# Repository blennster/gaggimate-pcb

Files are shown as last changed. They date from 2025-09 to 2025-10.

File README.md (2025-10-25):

This is a reimplemenation of the gaggimate PCB. It is not officaly supported and never will be.

This work is in no way affiliated with the https://gaggimate.eu/ project.

## License

This work is licensed under CC BY-NC-SA 4.0. To view a copy of this license, visit https://creativecommons.org/licenses/by-nc-sa/4.0/

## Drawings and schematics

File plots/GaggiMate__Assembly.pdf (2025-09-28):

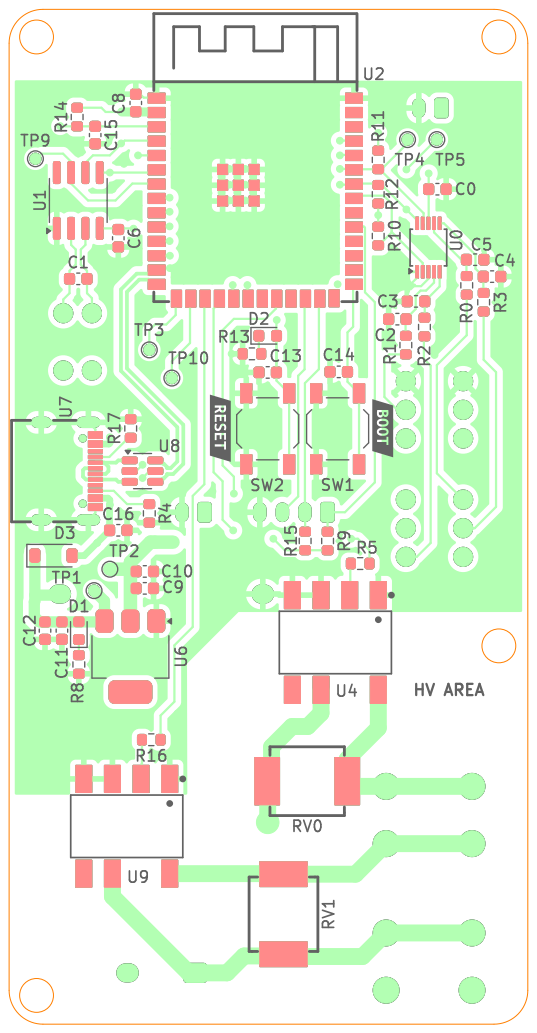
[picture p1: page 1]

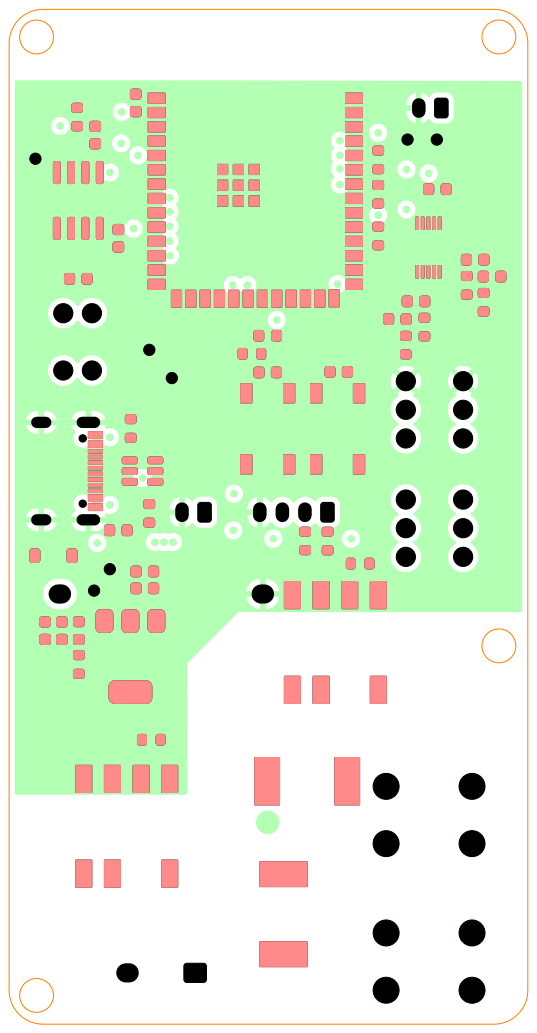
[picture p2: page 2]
D Date: KiCad; E.D.A. 9.0.4 Size: A4; Rev:; Id: /1 Title: File: GaggiMate.kicad_pcb Sheet: Colored; TOP-Copy Board2Pdf:; Colored; TOP-Copy -; Page 2/4

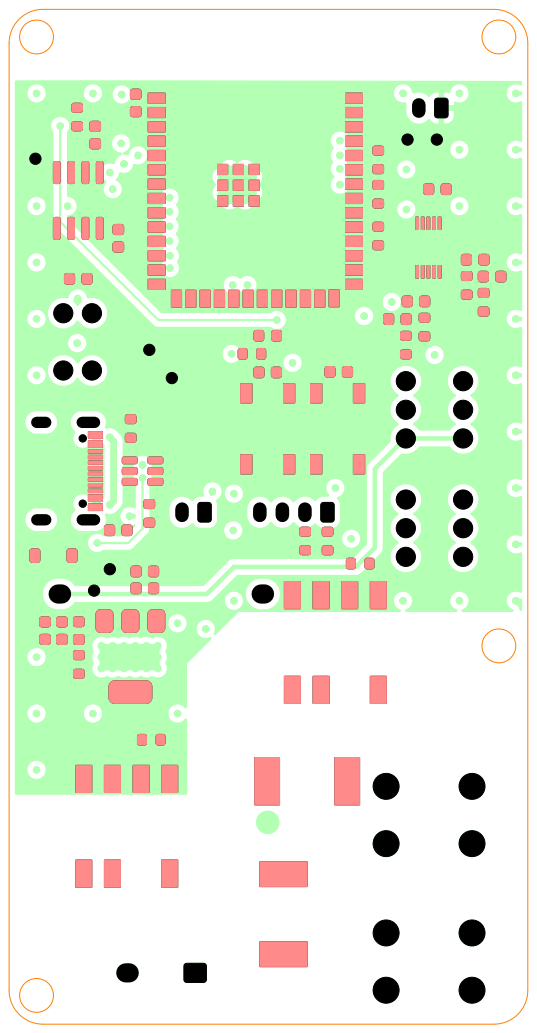
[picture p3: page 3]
D Date: KiCad; E.D.A. 9.0.4 Size: A4; Rev:; Id: /1 Title: File: GaggiMate.kicad_pcb Sheet: Colored; TOP-Copy-Copy Board2Pdf:; Colored; TOP-Copy-Copy; Page 3/4

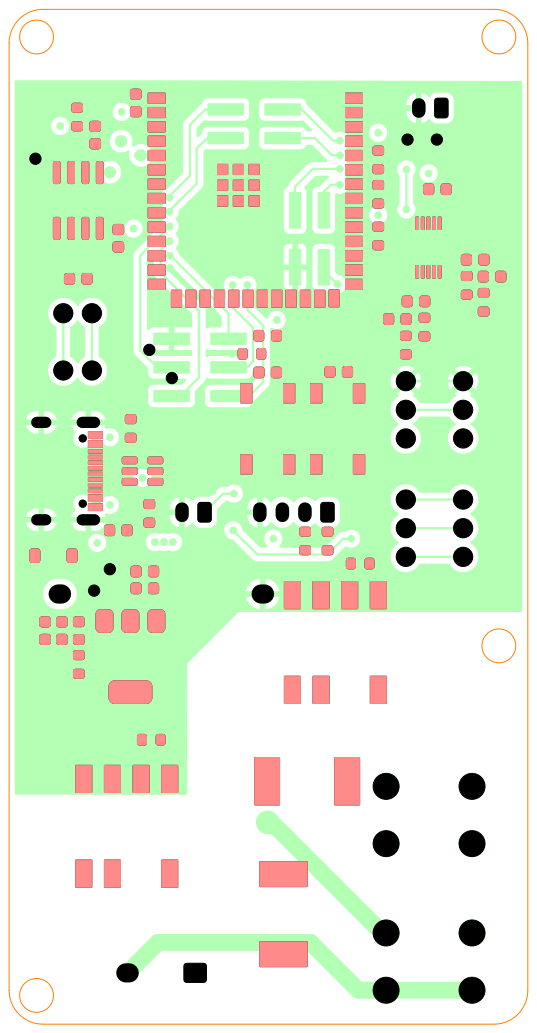
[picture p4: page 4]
D Date: KiCad; E.D.A. 9.0.4 Size: A4; Rev:; Id: /1 Title: File: GaggiMate.kicad_pcb Sheet: Colored; TOP-Copy-Copy-Copy Board2Pdf:; Colored; TOP-Copy-Copy-Copy; Page 4/4

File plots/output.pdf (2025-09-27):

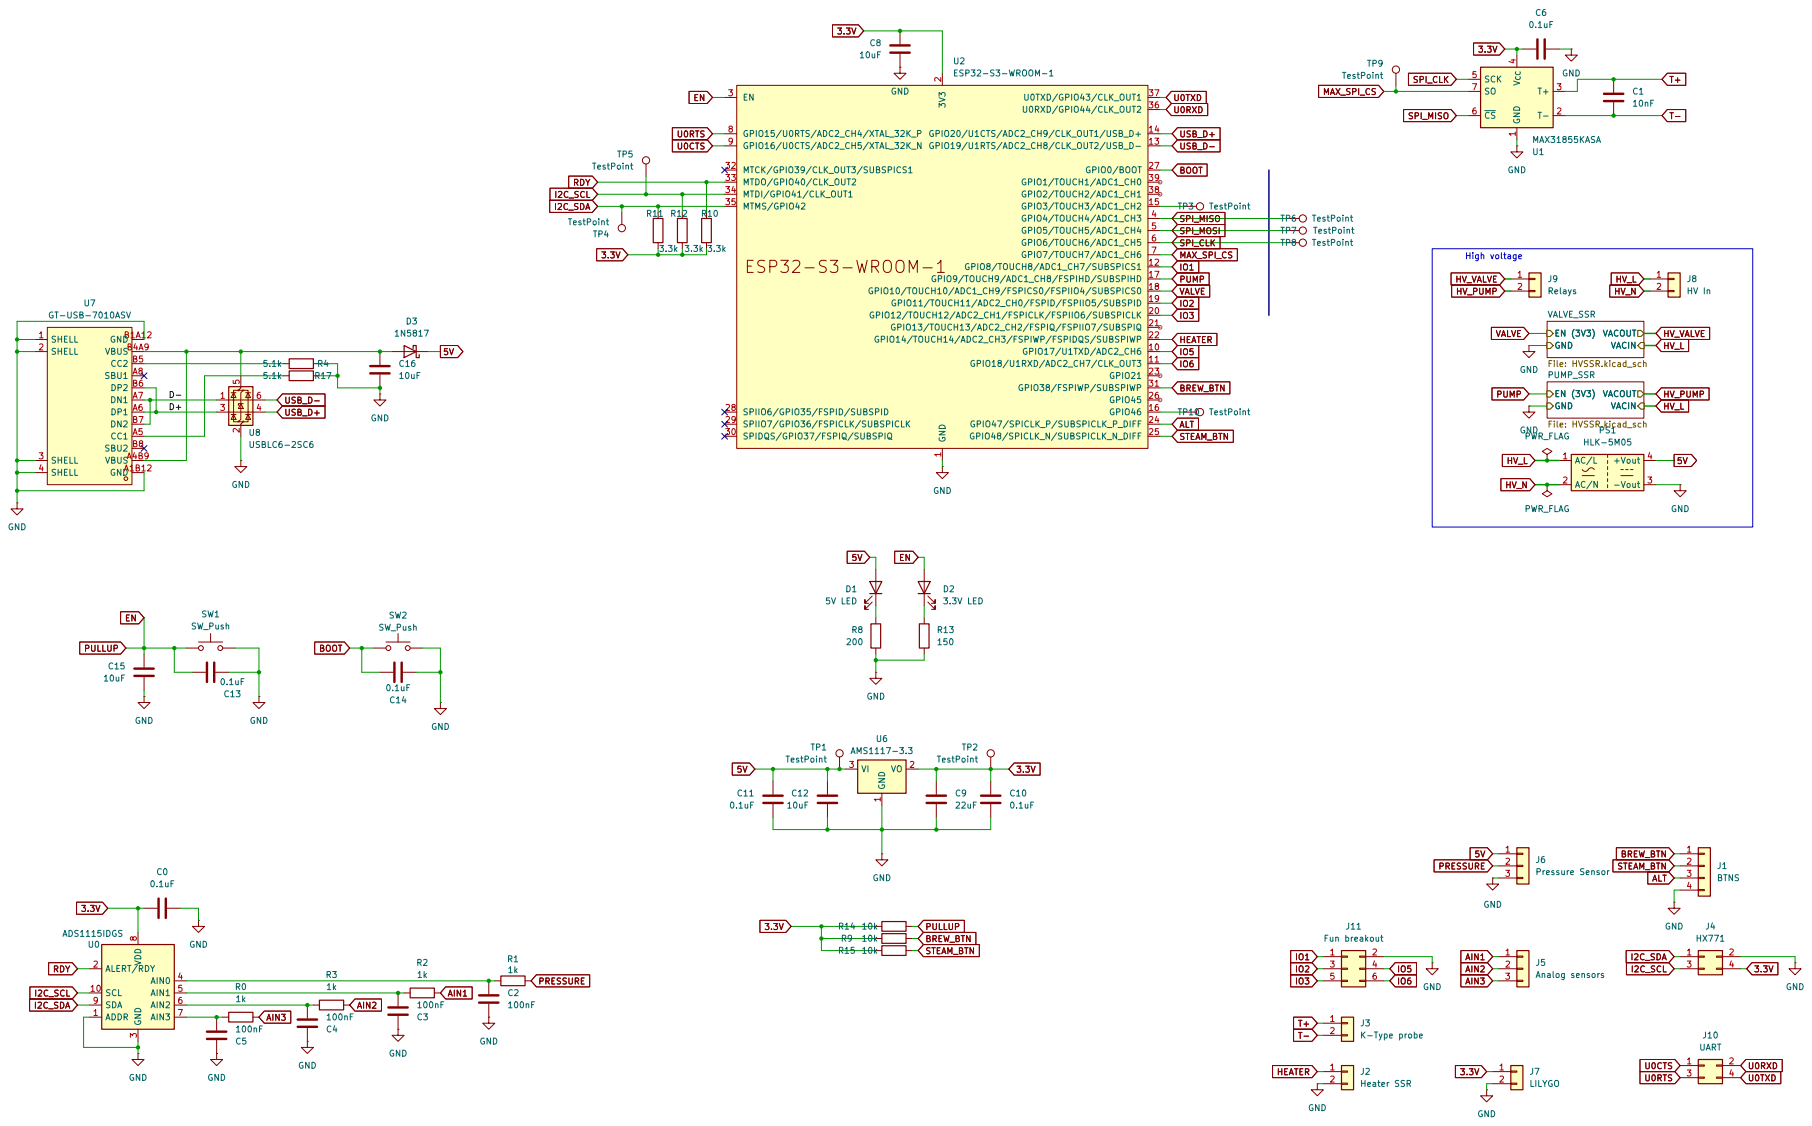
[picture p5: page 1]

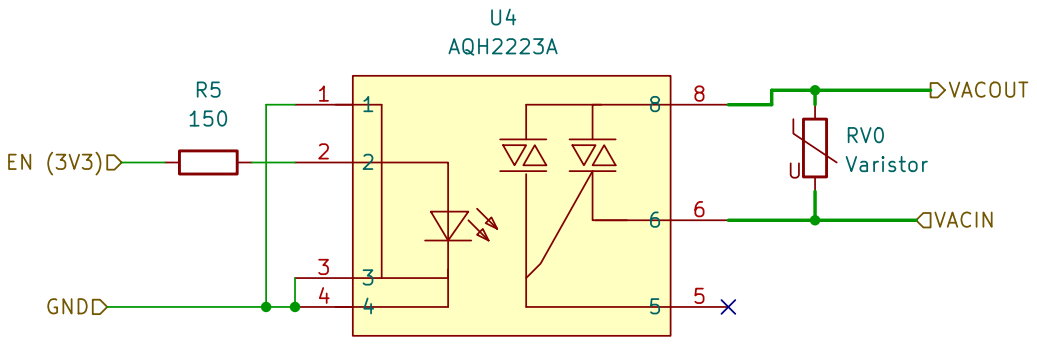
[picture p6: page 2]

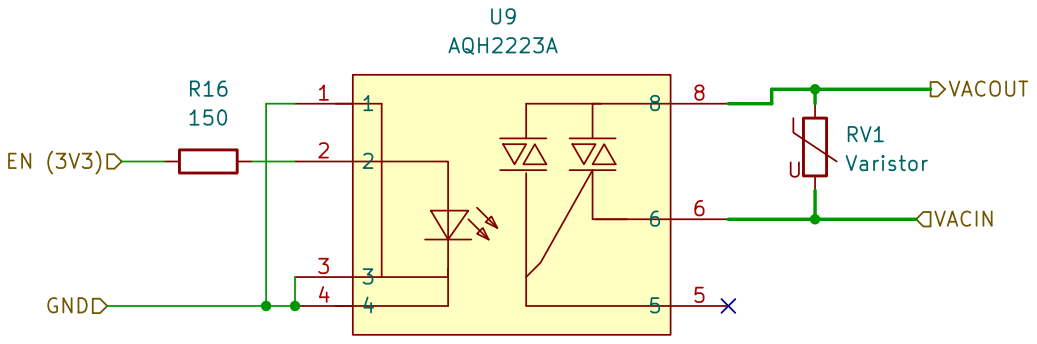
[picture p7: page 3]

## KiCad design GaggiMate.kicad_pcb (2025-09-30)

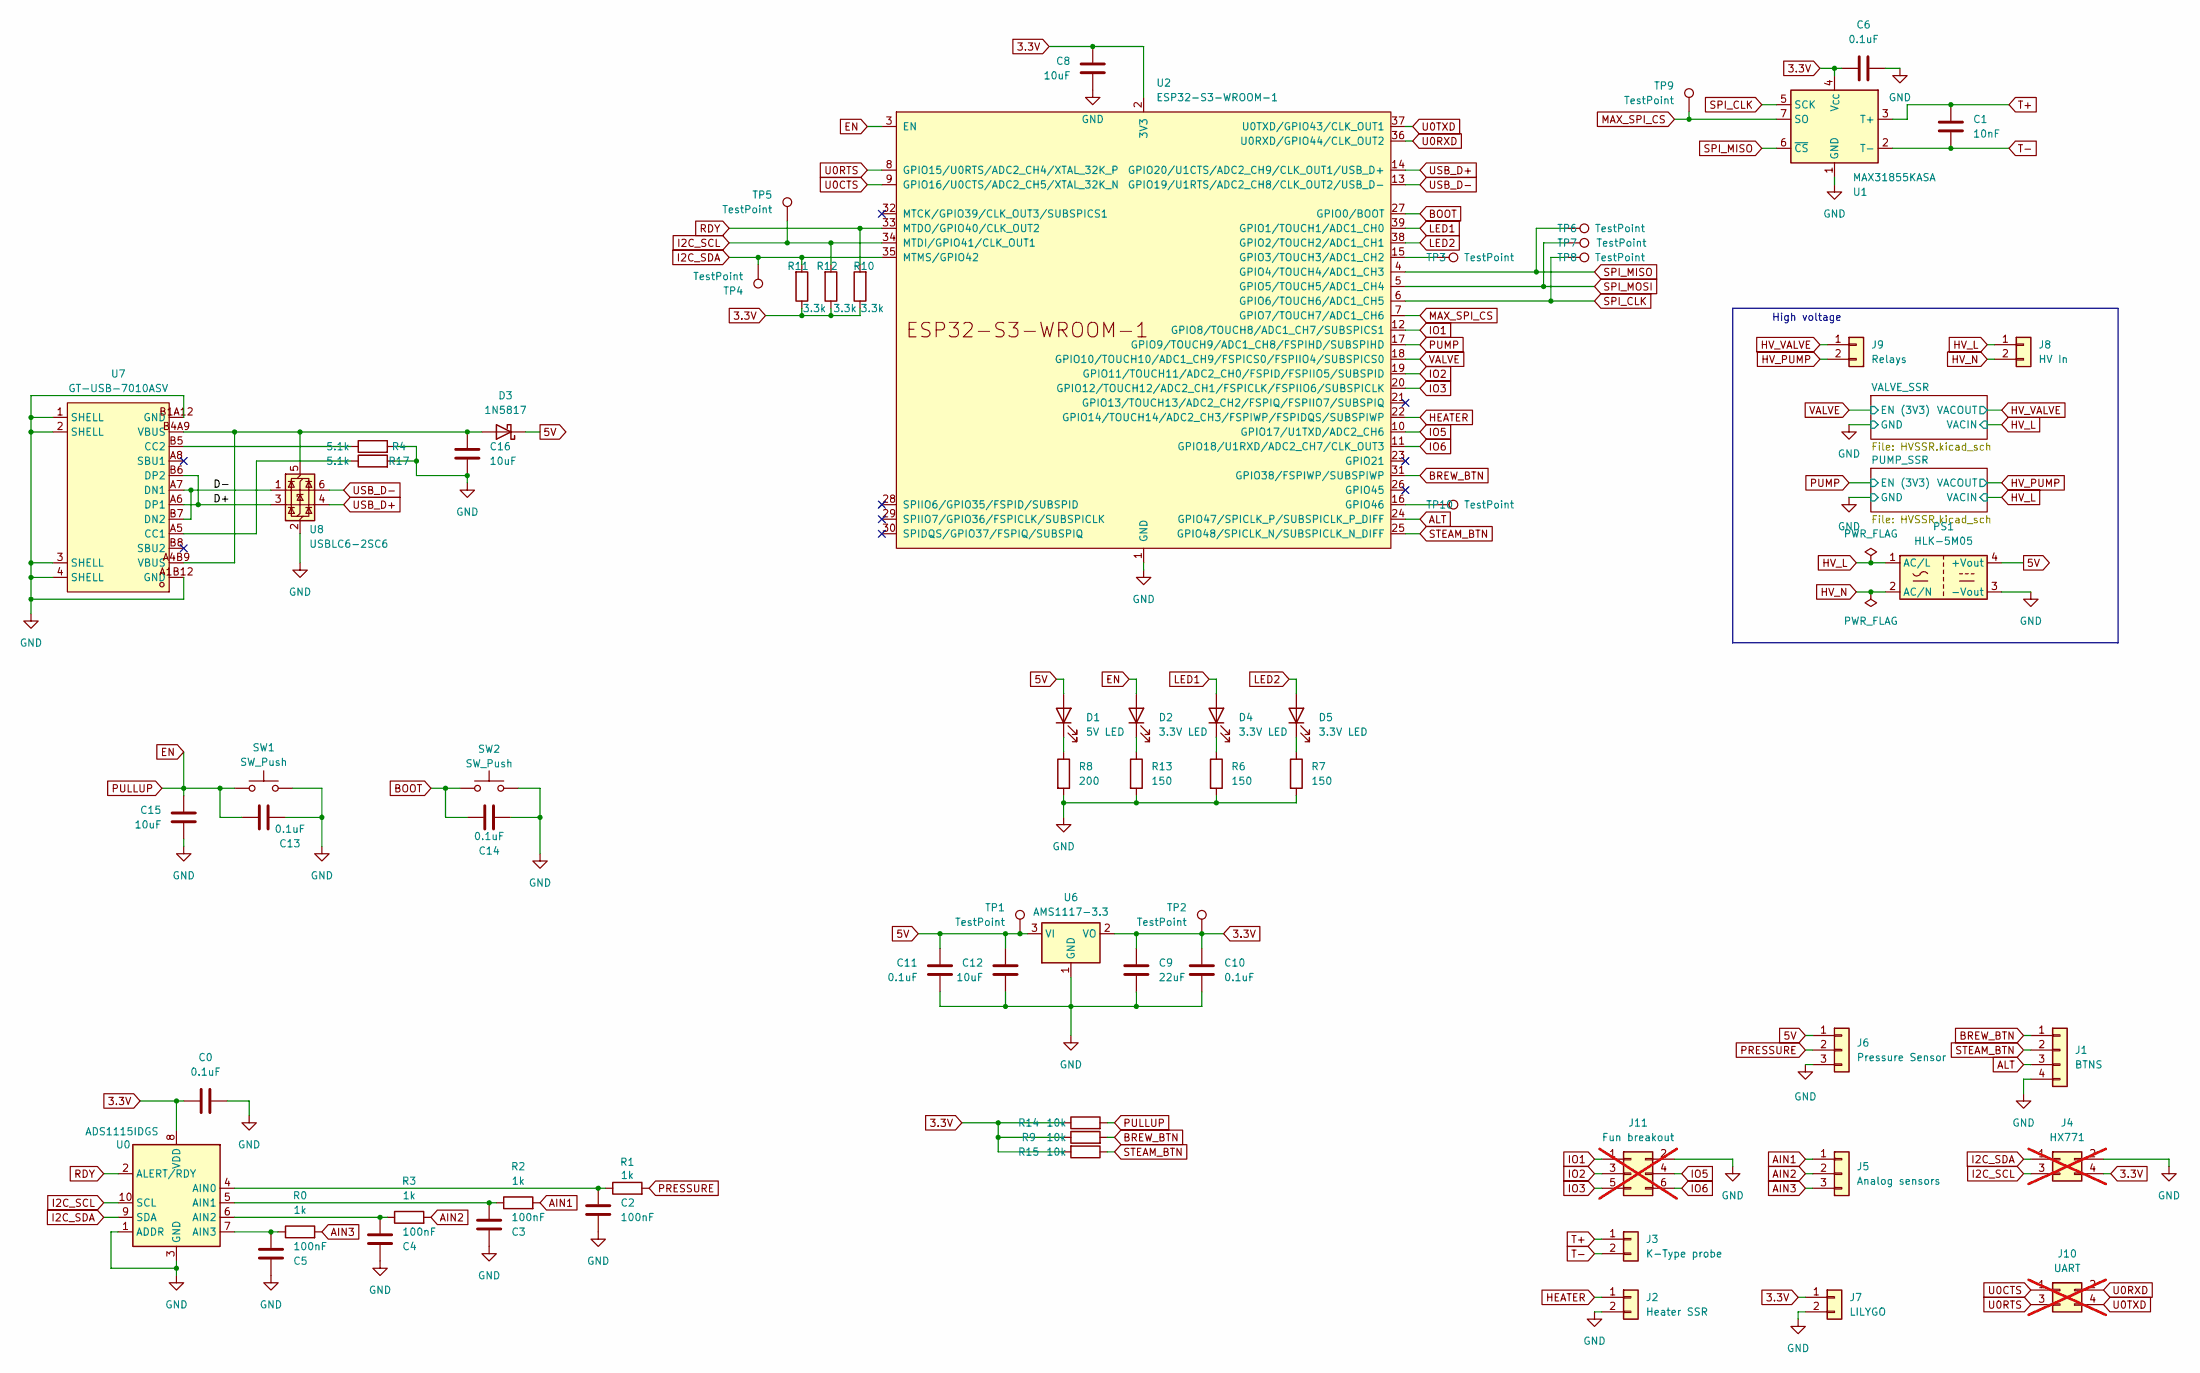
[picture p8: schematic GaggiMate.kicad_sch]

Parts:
C0, C6, C10, C11, C13, C14: 0.1uF; C_0603_1608Metric
C1: 10nF; C_0603_1608Metric
C2, C3, C4, C5: 100nF; C_0603_1608Metric
C8, C12, C15, C16: 10uF; C_0603_1608Metric
C9: 22uF; C_0603_1608Metric
D1: 5V LED; LED_0603_1608Metric
D2, D4, D5: 3.3V LED; LED_0603_1608Metric
D3: 1N5817; D_SOD-123
J1: BTNS; JST_PH_B4B-PH-K_1x04_P2.00mm_Vertical
J2: Heater SSR; JST_PH_B2B-PH-K_1x02_P2.00mm_Vertical
J3: K-Type probe; CONN-TH_2P-P2.54_DIBO_DB141V-2.54-2P
J4: HX771; PinHeader_2x02_P2.54mm_Vertical_SMD; not fitted
J5: Analog sensors; CONN-TH_3P-P2.54_DIBO_DB141V-2.54-3P
J6: Pressure Sensor; CONN-TH_3P-P2.54_DIBO_DB141V-2.54-3P
J7: LILYGO; JST_PH_B2B-PH-K_1x02_P2.00mm_Vertical
J8: HV In; CONN-TH_2P-P5.08_DIBO_DB142V-5.08-2P
J9: Relays; CONN-TH_2P-P5.08_DIBO_DB142V-5.08-2P
J10: UART; PinHeader_2x02_P2.54mm_Vertical_SMD; not fitted
J11: Fun breakout; PinHeader_2x03_P2.54mm_Vertical_SMD; not fitted
PS1: HLK-5M05; Converter_ACDC_Hi-Link_HLK-5Mxx
R0, R1, R2, R3: 1k; R_0603_1608Metric
R4, R17: 5.1k; R_0603_1608Metric
R6, R7, R13: 150; R_0603_1608Metric
R8: 200; R_0603_1608Metric
R9, R14, R15: 10k; R_0603_1608Metric
R10, R11, R12: 3.3k; R_0603_1608Metric
SW1, SW2: SW_Push; SW_SPST_TL3342
TP1, TP2, TP3, TP4, TP5, TP6, TP7, TP8, TP9, TP10: TestPoint; TestPoint_Pad_D1.0mm
U0: ADS1115IDGS; TSSOP-10_3x3mm_P0.5mm
U1: MAX31855KASA; SOIC-8_3.9x4.9mm_P1.27mm
U2: ESP32-S3-WROOM-1; WIRELM-SMD_ESP32-S3-WROOM-1
U6: AMS1117-3.3; SOT-223-3_TabPin2
U7: GT-USB-7010ASV; USB-C-SMD_G-SWITCH_GT-USB-7010ASV; LCSC Part C2988369
U8: USBLC6-2SC6; SOT-23-6

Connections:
3.3V: C0.1, C6.1, C8.2, C9.1, C10.1, J4.4, J7.1, R9.1, R10.1, R11.1, R12.1, R14.1, R15.2, TP2.1, U0.8 (VDD), U1.4 (V_{CC}), U2.2 (3V3), U6.2 (VO)
5V: C11.2, C12.1, D1.2 (A), D3.1 (K), J6.1, PS1.4 (+Vout), TP1.1, U6.3 (VI)
/D+: U7.A6 (DP1), U7.B6 (DP2), U8.3 (I/O2)
/D-: U7.A7 (DN1), U7.B7 (DN2), U8.1 (I/O1)
AIN1: J5.1, R2.2
AIN2: J5.2, R3.2
AIN3: J5.3, R0.2
ALT: J1.3, U2.24 (GPIO47/SPICLK_P/SUBSPICLK_P_DIFF)
BOOT: C14.1, SW2.1, U2.27 (GPIO0/BOOT)
BREW_BTN: J1.1, R9.2, U2.31 (GPIO38/FSPIWP/SUBSPIWP)
EN: C13.1, C15.1, D2.2 (A), R14.2, SW1.1, U2.3 (EN)
GND: C0.2, C2.2, C3.1, C4.1, C5.1, C6.2, C8.1, C9.2, C10.2, C11.1, C12.2, C13.2, C14.2, C15.2, C16.2, J1.4, J2.2, J4.2, J6.3, J7.2, J11.2, PS1.3 (-Vout), R4.2, R6.2, R7.2, R8.2, R13.2, R17.2, SW1.2, SW2.2, U0.1 (ADDR), U0.3 (GND), U1.1 (GND), U2.1 (GND), U2.40 (GND), U2.41 (GND), U6.1 (GND), U7.1 (SHELL), U7.2 (SHELL), U7.3 (SHELL), U7.4 (SHELL), U7.A1B12 (GND), U7.B1A12 (GND), U8.2 (GND); also elsewhere on the board
HEATER: J2.1, U2.22 (GPIO14/TOUCH14/ADC2_CH3/FSPIWP/FSPIDQS/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)
HV_L: J8.1, PS1.1 (AC/L); also elsewhere on the board
HV_N: J8.2, PS1.2 (AC/N)
HV_PUMP: J9.2; also elsewhere on the board
HV_VALVE: J9.1; also elsewhere on the board
I2C_SCL: J4.3, R12.2, TP5.1, U0.10 (SCL), U2.34 (MTDI/GPIO41/CLK_OUT1)
I2C_SDA: J4.1, R11.2, TP4.1, U0.9 (SDA), U2.35 (MTMS/GPIO42)
IO1: J11.1, U2.12 (GPIO8/TOUCH8/ADC1_CH7/SUBSPICS1)
IO2: J11.3, U2.19 (GPIO11/TOUCH11/ADC2_CH0/FSPID/FSPIIO5/S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)
IO3: J11.5, U2.20 (GPIO12/TOUCH12/ADC2_CH1/FSPICLK/FSPIIO6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)
IO5: J11.4, U2.10 (GPIO17/U1TXD/ADC2_CH6)
IO6: J11.6, U2.11 (GPIO18/U1RXD/ADC2_CH7/CLK_OUT3)
LED1: D4.2 (A), U2.39 (GPIO1/TOUCH1/ADC1_CH0)
LED2: D5.2 (A), U2.38 (GPIO2/TOUCH2/ADC1_CH1)
MAX_SPI_CS: TP9.1, U1.7 (SO), U2.7 (GPIO7/TOUCH7/ADC1_CH6)
unnamed: D1.1 (K), R8.1
unnamed: D2.1 (K), R13.1
unnamed: C16.1, D3.2 (A), U7.A4B9 (VBUS), U7.B4A9 (VBUS), U8.5 (VBUS)
unnamed: D4.1 (K), R6.1
unnamed: D5.1 (K), R7.1
unnamed: C2.1, R1.1, U0.4 (AIN0)
unnamed: C3.2, R2.1, U0.5 (AIN1)
unnamed: C4.2, R3.1, U0.6 (AIN2)
unnamed: C5.2, R0.1, U0.7 (AIN3)
unnamed: TP3.1, U2.15 (GPIO3/TOUCH3/ADC1_CH2)
unnamed: TP10.1, U2.16 (GPIO46)
unnamed: R17.1, U7.A5 (CC1)
unnamed: R4.1, U7.B5 (CC2)
PRESSURE: J6.2, R1.2
PUMP: U2.17 (GPIO9/TOUCH9/ADC1_CH8/FSPIHD/SUBSPIHD); also elsewhere on the board
RDY: R10.2, U0.2 (ALERT/RDY), U2.33 (MTDO/GPIO40/CLK_OUT2)
SPI_CLK: TP8.1, U1.5 (SCK), U2.6 (GPIO6/TOUCH6/ADC1_CH5)
SPI_MISO: TP6.1, U1.6 (~CS), U2.4 (GPIO4/TOUCH4/ADC1_CH3)
SPI_MOSI: TP7.1, U2.5 (GPIO5/TOUCH5/ADC1_CH4)
STEAM_BTN: J1.2, R15.1, U2.25 (GPIO48/SPICLK_N/SUBSPICLK_N_DIFF)
T+: C1.1, J3.1, U1.3 (T+)
T-: C1.2, J3.2, U1.2 (T-)
U0CTS: J10.1, U2.9 (GPIO16/U0CTS/ADC2_CH5/XTAL_32K_N)
U0RTS: J10.3, U2.8 (GPIO15/U0RTS/ADC2_CH4/XTAL_32K_P)
U0RXD: J10.2, U2.36 (U0RXD/GPIO44/CLK_OUT2)
U0TXD: J10.4, U2.37 (U0TXD/GPIO43/CLK_OUT1)
USB_D+: U2.14 (GPIO20/U1CTS/ADC2_CH9/CLK_OUT1/USB_D+), U8.4 (I/O2)
USB_D-: U2.13 (GPIO19/U1RTS/ADC2_CH8/CLK_OUT2/USB_D-), U8.6 (I/O1)
VALVE: U2.18 (GPIO10/TOUCH10/ADC1_CH9/FSPICS0/FSPIIO4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); also elsewhere on the board

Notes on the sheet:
High voltage

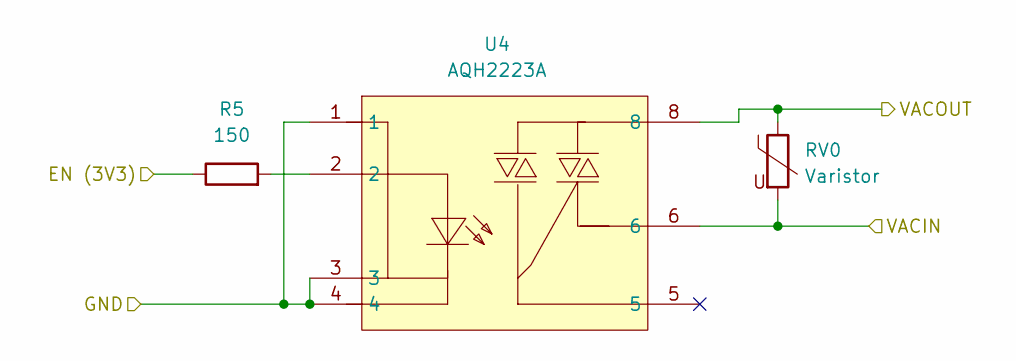
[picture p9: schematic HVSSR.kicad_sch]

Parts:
R5: 150; R_0603_1608Metric
RV0: Varistor; RES-SMD_L6.8-W5.9-LS7.8
U4: AQH2223A; SMD-8_7P-L9.8-W6.4-P2.54-BL-PE7; LCSC Part C153026

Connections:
GND: U4.1, U4.3, U4.4; also elsewhere on the board
HV_L: RV0.2, U4.6; also elsewhere on the board
HV_VALVE: RV0.1, U4.8; also elsewhere on the board
unnamed: R5.2, U4.2
VALVE: R5.1; also elsewhere on the board

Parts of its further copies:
R16: 150; R_0603_1608Metric
RV1: Varistor; RES-SMD_L6.8-W5.9-LS7.8
U9: AQH2223A; SMD-8_7P-L9.8-W6.4-P2.54-BL-PE7; LCSC Part C153026

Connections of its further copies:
GND: U9.1, U9.3, U9.4; also elsewhere on the board
HV_L: RV1.2, U9.6; also elsewhere on the board
HV_PUMP: RV1.1, U9.8; also elsewhere on the board
unnamed: R16.2, U9.2
PUMP: R16.1; also elsewhere on the board

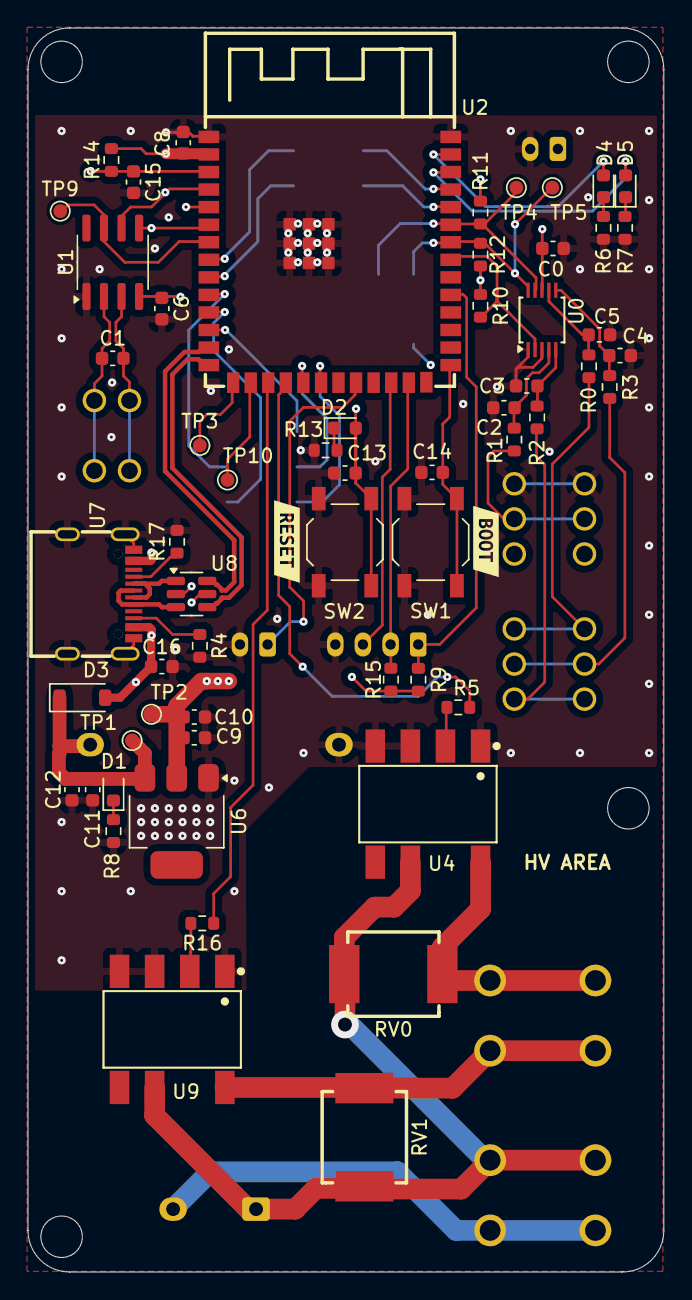
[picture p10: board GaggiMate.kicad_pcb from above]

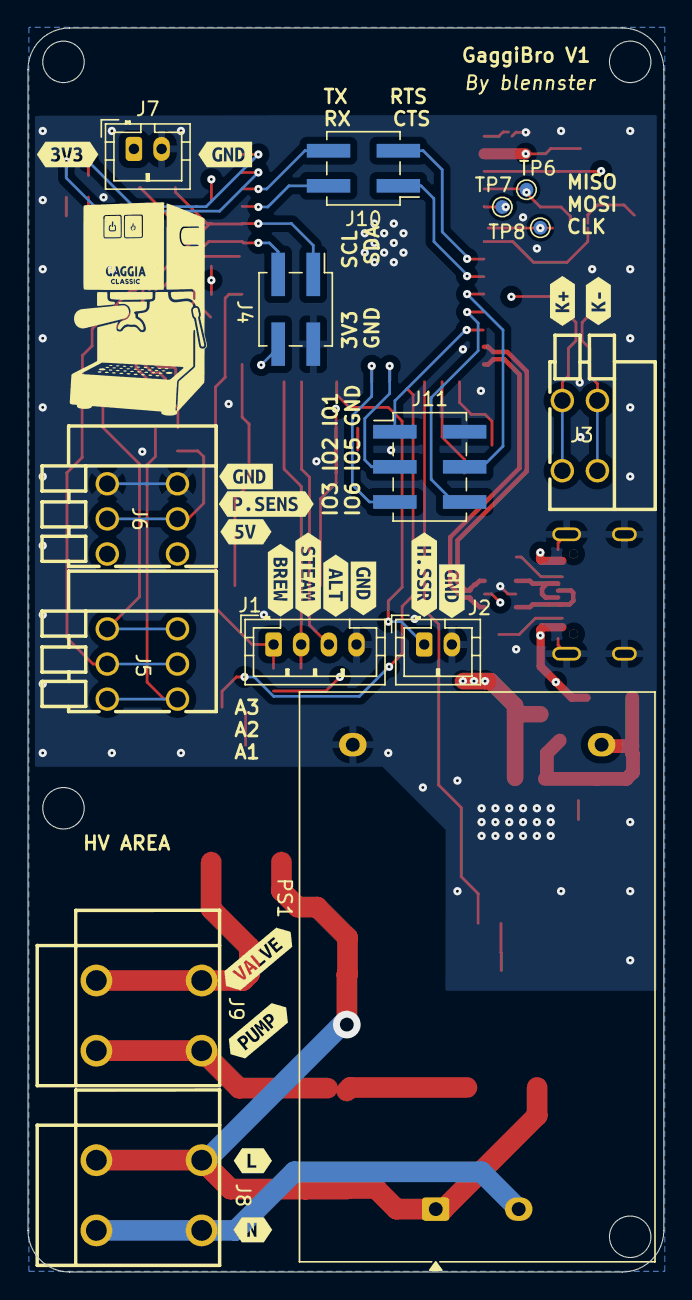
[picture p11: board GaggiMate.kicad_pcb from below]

Board: 4 copper layers, 46.0 x 90.0 mm, 92 parts (32 on the bottom side), 58 nets.

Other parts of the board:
kibuzzard-68D85A7C: G***; kibuzzard-68D85A7C
kibuzzard-68D85A63: G***; kibuzzard-68D85A63
kibuzzard-68D85AF0: G***; kibuzzard-68D85AF0
kibuzzard-68D85B00: G***; kibuzzard-68D85B00
kibuzzard-68D853DB, kibuzzard-68D853DB#2: G***; kibuzzard-68D853DB
kibuzzard-68D858A7: G***; kibuzzard-68D858A7
kibuzzard-68D858C6: G***; kibuzzard-68D858C6
kibuzzard-68D859D6: G***; kibuzzard-68D859D6
kibuzzard-68D8588D: G***; kibuzzard-68D8588D
kibuzzard-68D8589E: G***; kibuzzard-68D8589E
kibuzzard-68D8595E: G***; kibuzzard-68D8595E
kibuzzard-68D85755: G***; kibuzzard-68D85755
kibuzzard-68D85864: G***; kibuzzard-68D85864
kibuzzard-68D85872: G***; kibuzzard-68D85872
kibuzzard-68D85884: G***; kibuzzard-68D85884
kibuzzard-68D85899: G***; kibuzzard-68D85899
kibuzzard-68D85940: G***; kibuzzard-68D85940
kibuzzard-68D85954: G***; kibuzzard-68D85954

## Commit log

2025-09-18 inital commit
    [GaggiMate.kicad_pcb, GaggiMate.kicad_sch]
2025-09-18 updated power and began 5-3v regulator
    [GaggiMate.kicad_sch]
2025-09-19 bunch of updates
    added:
    - relays
    - barrel jack
    - more proper routing
    [GaggiMate.kicad_pcb, GaggiMate.kicad_sch, MyRelay.kicad_sch]
2025-09-20 attempt a HV stepdown and some PCB stuff
    [GaggiMate.kicad_pcb, GaggiMate.kicad_sch, HVSupply.kicad_sch]
2025-09-20 update footprints, add 230v module, use SSRs and do some basic layouting
    [GaggiMate.kicad_pcb, GaggiMate.kicad_sch, HVSSR.kicad_sch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]
2025-09-21 update some footprints etc
    [GaggiMate.kicad_pcb, GaggiMate.kicad_sch, HVSSR.kicad_sch]
2025-09-22 Moved front side components to other board, finished cap and resistor selection and maybe finalizing layout
    [ExtraComponents.kicad_sch, GaggiMate.kicad_pcb, GaggiMate.kicad_sch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]
2025-09-22 geographical referencing instead
    [GaggiMate.kicad_pcb, GaggiMate.kicad_sch, HVSSR.kicad_sch]
2025-09-22 attempt some routing
    [GaggiMate.kicad_pcb, GaggiMate.kicad_sch, HVSSR.kicad_sch]
2025-09-23 update analog filters and started some HV traces
    [GaggiMate.kicad_pcb, GaggiMate.kicad_sch]
2025-09-23 more routing and and programming buttons
    [GaggiMate.kicad_pcb, GaggiMate.kicad_sch]
2025-09-24 update layout a lot
    [GaggiMate.kicad_pcb]
2025-09-24 finalize layout and tracks?
    [GaggiMate.kicad_pcb, GaggiMate.kicad_sch]
2025-09-27 some updates
    [GaggiMate.kicad_pcb, GaggiMate.kicad_sch]
2025-09-27 release candidate 1
    [GaggiMate.kicad_pcb, GaggiMate.kicad_sch]
2025-09-27 add custom silkscreen and missing lilygo out pins
    [GaggiMate.kicad_pcb, GaggiMate.kicad_sch, HVSSR.kicad_sch]
2025-09-27 make ready for release
    [GaggiMate.kicad_pcb]
2025-09-28 update to new footprint ad make stuff nice
    [GaggiMate.kicad_pcb, GaggiMate.kicad_sch]
2025-09-29 add missing models and finalize pcb
    [GaggiMate.kicad_pcb, GaggiMate.kicad_sch]
2025-09-29 released version
    [GaggiMate.kicad_pcb, GaggiMate.kicad_sch]
2025-09-30 Swap GND and 5V as they were mislabled
    [GaggiMate.kicad_pcb]
